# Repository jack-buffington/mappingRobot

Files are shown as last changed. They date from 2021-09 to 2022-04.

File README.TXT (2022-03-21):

This readme was last updated on March 20 2022.

This repository will eventually contain all of the files necessary to make a mapping robot that can map its 
environment using a 2D lidar-like sensor.  At the time of writing this README, the project is 
ongoing.  Eventual goals of this project are:

* Have the robot autonomously map its environment using a RPlidar A2 module.  
* Know when it is done mapping its environment. 
* Do so using ROS.  
* With only a few minor exceptions, run exclusively my own code.
* Have the capability to connect to the robot using a remote computer which can view the current state of the
map as well as to take direct control of the robot.  

The robot system will consist of three processors.  The first is the remote computer which does no 
major computation.  It will be for the user to view the map and to control the state of the robot if necessary.  
The second is an onboard processor that will do the heavy lifting and which holds 
the most up-to-date map.  The third is a microcontroller that handles low-level tasks such as driving the motors, 
reading sensors, and controllng the power to the motors, CPU, and itself. 

Power is supplied to the robot from an off-the-shelf battery pack for Dewalt cordless tools.  

It its current state, the MCU code is pretty much fully functional.  I will likely update it at some point to
read one or more downward-looking range finders so that it doesn't attempt suicide by driving down steps.  It currently
can do the following:
   * Read the battery voltage, display it on the OLED display, and send the voltage to the CPU
   * Read the encoders attached to the motors and send their values to the CPU
   * Drive the motors with a closed-loop velocity controller
   * Play beeps
   * Control the power to the CPU, motors, and itself
   * Communicate through two serial ports.  One to the CPU and one connected to the programming port.
  
The CPU code has:
   RPlidar node - controls a RPlidar A2 and reads its data.  This data is conditionally published based on a divider that 
       Allows it to send every N scans.  
   MCU node - Subscribes to a few topics which can be forwarded to the MCU and publishes a couple others which repeat 
       messages received from the MCU in a ROS-friendly format.  

The Remote computer code has:
   lidar viewer - Ideally I would use RVIZ to see the lidar data but either I don't yet know how to use RVIZ or I have it
	misconfigured so I wrote a quick and dirty program to display the scans.  
   joystick driving node - Lets you control the robot with a joystick if you have teleop_twist_joy installed on your system.

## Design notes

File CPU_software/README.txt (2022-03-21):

To compile, enter the following from this directory:

bash ./compileIt.sh

That script sets the date in case it is wrong so that colcon doesn't complain.  It also deletes previous build files 
so that you end up with something that is based on your most recent code.  It then does the compile.

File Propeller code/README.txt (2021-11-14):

Although they aren't used here, I have also included velocityPID.spin and velocityWithAccelerationTester.spin just for reference.

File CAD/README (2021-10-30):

You can find the most recent CAD model here:
https://cad.onshape.com/documents/e171561c6562339657e2c6d4/w/af4afc644c5b7dbe0063a584/e/c5b0ace67d7282b7c7552f78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

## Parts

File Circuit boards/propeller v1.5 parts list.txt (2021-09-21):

Partlist

Exported from Propeller board rev 1.5.brd at 7/13/2021 8:17 PM

EAGLE Version 9.2.2 Copyright (c) 1988-2018 Autodesk, Inc.

Assembly variant: 

Part                         Value                                            Package                              Library               Position (mil)        Orientation

3.3V_LED                                                                      LED_SML1206                          arduino board rev 1.3 (164 433)             R90
3V3_REGULATOR_FOR_PROPELLER  VOLTAGE_REGULATOR_3_TERMINALXP_POWER_VR05_SERIES VR05_SERIES_VREG                     Jack                  (1717.40157 1269.37008) R180
5V_C_680PF                   680pf                                            JACK_0805                            arduino board rev 1.3 (3220 945)            R180
5V_LED                                                                        LED_SML1206                          arduino board rev 1.3 (2595 945)            R0
5V_LED_R1                    470                                              JACK_0805                            arduino board rev 1.3 (2820 945)            R0
5V_LED_R2                    470                                              JACK_0805                            arduino board rev 1.3 (256 472)             R270
5V_REGULATOR_PULLUP          10K                                              JACK_0805                            arduino board rev 1.3 (3370 1495)           R180
5V_R_220                     220                                              JACK_0805                            arduino board rev 1.3 (3370 945)            R0
BATTERY_VOLTAGE_DIVIDER_HIGH 11K                                              JACK_0805                            arduino board rev 1.3 (2047.42188 1209.86897) R90
BATTERY_VOLTAGE_DIVIDER_LOW  1.6K                                             JACK_0805                            arduino board rev 1.3 (2046.38521 1378.2687) R90
MOTOR_C_680PF                680pf                                            JACK_0805                            arduino board rev 1.3 (3214.46088 289.96518) R180
MOTOR_ENABLE_MOSFET          JACK_MOSFET_N_CHANNELBSS138LCT-ND                JACK_SOT23                           arduino board rev 1.3 (3630.98425 571.22047) R0
MOTOR_ENABLE_MOSFET1         JACK_MOSFET_N_CHANNELBSS138LCT-ND                JACK_SOT23                           arduino board rev 1.3 (3620 1270)           R0
MOTOR_LED                                                                     LED_SML1206                          arduino board rev 1.3 (2595 295)            R0
MOTOR_LED_R                  600                                              JACK_0805                            arduino board rev 1.3 (2820 295)            R0
MOTOR_MOSFET_PULLDOWN        10K                                              JACK_0805                            arduino board rev 1.3 (3630.98425 453.11024) R180
MOTOR_PULLUP                 10K                                              JACK_0805                            arduino board rev 1.3 (3358.70079 845.94488) R180
MOTOR_PULLUP2                10K                                              JACK_0805                            arduino board rev 1.3 (3620 1145)           R180
MOTOR_R_220                  220                                              JACK_0805                            arduino board rev 1.3 (3364.46088 289.96518) R0
MOTOR_TRIM                   13.2K                                            JACK_0805                            arduino board rev 1.3 (3050 290)            R0
R1                           240                                              805_SMD                              jack_custom           (250 314)             R90
R25                          10k                                              805_SMD                              jack_custom           (1170 920)            R0
RTRIM_5V                     16.2K                                            JACK_0805                            arduino board rev 1.3 (3051.48413 945)      R0
U$1                          CONNECTOR_2_PINJST_PH_SERIES                     JST_2_PIN_PH_SERIES                  Jack                  (2160 340)            R180
U$2                          JACK_SCREW_TERMINAL_2_CONDUCTORAMP-282837-2      JACK_AMP-282837-2                    arduino board rev 1.3 (3045 1720)           R0
U$3                          POWER_CONTROLLER_LTC2954-2TSOT-23-8              TSOT-23-8                            Jack                  (2029 479)            R0
U$4                          JACK_DC_TO_DC_VARIABLE_555-1172-1-ND             JACK_DC2DC_555-1172-1-ND             arduino board rev 1.3 (3520 1445)           R180
U$5                          1uf                                              0805                                 Jack                  (2195 470)            R180
U$6                          JACK_SCREW_TERMINAL_2_CONDUCTORAMP-282837-2      JACK_AMP-282837-2                    arduino board rev 1.3 (2345 1720)           R180
U$7                          100K                                             0805                                 Jack                  (2145 620)            R90
U$9                          100K                                             0805                                 Jack                  (2220 620)            R90
U$10                         10K                                              0805                                 Jack                  (1937 634)            R180
U$11                         1000pf                                           0805                                 Jack                  (1190 1240)           R270
U$12                         MOSFET_P_CHANNELSI4431CDY                        SO8                                  Jack                  (2120 920)            R0
U$13                         JACK_SCREW_TERMINAL_2_CONDUCTORAMP-282837-2      JACK_AMP-282837-2                    arduino board rev 1.3 (3720 1720)           R0
U$14                         .1uf                                             0805                                 Jack                  (340 314)             R90
U$15                         CRYSTAL8X4.5_PACKAGE                             CRYSTAL_NX8045GB-5MHZ-STD-CSF-3      Jack                  (800 500)             R270
U$16                         .1uf                                             0805                                 Jack                  (360 1060)            R270
U$17                         JACK_DC_TO_DC_VARIABLE_555-1172-1-ND             JACK_DC2DC_555-1172-1-ND             arduino board rev 1.3 (3520 795)            R180
U$18                         .1uf                                             0805                                 Jack                  (1580 1420)           R0
U$19                         TEST_POINT                                       KEYSTONE_ELECTRONICS_5118_TEST_POINT Jack                  (3670 920)            R0
U$20                         LED0805                                          0805                                 Jack                  (340 474)             R270
U$21                         HEADER_4_PIN_.1"                                 FOUR_.1"_HOLES                       Jack                  (390 740)             R90
U$22                         HEADER_5X2                                       HEADER_5X2_.1"_SPACING               Jack                  (820 1720)            R90
U$23                         CONNECTOR_4_PINJST_PH_SERIES                     JST_4_PIN_PH_SERIES                  Jack                  (1440 370)            R270
U$24                         CONNECTOR_4_PINJST_PH_SERIES                     JST_4_PIN_PH_SERIES                  Jack                  (1230 370)            R270
U$25                         CONNECTOR_4_PINJST_PH_SERIES                     JST_4_PIN_PH_SERIES                  Jack                  (1650 370)            R270
U$26                         CONNECTOR_2_PINJST_.1"                           JST_2_PIN_.1"                        Jack                  (2160 180)            R180
U$27                         10K                                              0805                                 Jack                  (1489 703)            R90
U$28                         10uF                                             1210                                 Jack                  (2470 670)            R90
U$29                         10uF                                             1210                                 Jack                  (2470 1320)           R90
U$30                         10uf                                             1210                                 Jack                  (2470 1120)           R270
U$31                         10uf                                             1210                                 Jack                  (2620 1320)           R90
U$32                         10uf                                             1210                                 Jack                  (2470 470)            R270
U$33                         10uf                                             1210                                 Jack                  (2620 1120)           R270
U$34                         SPEAKERGT-0950RP3                                AUDIO_TRANSDUCER_GT-0950RP3          Jack                  (1720 800)            R90
U$35                         DIODESOD-23/SC-76                                SOD-323/SC-76                        Jack                  (1490 870)            R90
U$36                         TRANSISTOR_NPNMMBT3904                           SOT23                                Jack                  (1340 710)            R180
U$37                         200                                              0805                                 Jack                  (1340 810)            R0
U$38                         CONNECTOR_3_PIN.1"SPACING                        THREE_.1"_HOLES                      Jack                  (3610 170)            R180
U$40                         10uf                                             1210                                 Jack                  (2620 470)            R270
U$41                         10uf                                             1210                                 Jack                  (2620 670)            R90
U$42                         1000pf                                           0805                                 Jack                  (1265 1240)           R90
U$43                         150K                                             0805                                 Jack                  (1120 1320)           R90
U$44                         100K                                             0805                                 Jack                  (1044 1320)           R270
U$45                         CONNECTOR_4_PINJST_PH_SERIES                     JST_4_PIN_PH_SERIES                  Jack                  (1020 370)            R270
U$46                         CONNECTOR_4_PINJST_PH_SERIES                     JST_4_PIN_PH_SERIES                  Jack                  (1670 1670)           R90
U$47                         CONNECTOR_4_PINJST_PH_SERIES                     JST_4_PIN_PH_SERIES                  Jack                  (570 370)             R270
U$48                         PROPELLER_PROGRAMMING_HEADERHOLES                FOUR_.1"HOLES                        Jack                  (1370 1070)           R270
U$49                         CONNECTOR_4_PINJST_PH_SERIES                     JST_4_PIN_PH_SERIES                  Jack                  (1900 1670)           R90
U1                           PARALLAX_PROPELLER                               44LQFP                               jack_custom           (770 1070)            R270
U2                           EEPROM_24XX256                                   8_MSOP                               jack_custom           (1170 770)            R0

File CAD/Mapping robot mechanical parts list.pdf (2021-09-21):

Quantity | Description | part number | Where to order | Alternate order location | Notes
2 Encoder/motor/gearbox combo | TT Motor with Encoder (6V 160RPM 120:1) | https://www.dfrobot.com/product-1457.html?search=TT%20Motor%20with%20Encoder%20%286V%20160RPM%20120%3A1%29
2 Wheels | https://www.dfrobot.com/product-352.html
1 1/4" black acrylic | https://www.amazon.com/gp/product/B01DYSTH3K
8 1 5/8" standoffs | https://www.mcmaster.com/91115A564
4 1" standoffs | https://www.mcmaster.com/91115A133
28 6-32 machine screws | https://www.mcmaster.com/92949A149
4 M3 machine screws | https://www.mcmaster.com/92000A120
4 6-32 lock nuts | https://www.mcmaster.com/91831A007
1 Caster | https://www.amazon.com/gp/product/B010SLSK48
2 motor mounts | https://www.pololu.com/product/2670https://www.robotshop.com/en/solarbotics-gmb39-gear-motor-bracket.html I scavenged my motor mounts from another project. Here are two mounts that I think would work but which aren't like the ones that I am using. You will need to adjust your CAD files to have the mounting holes be in the right places.
4 motor mount screws | Choose these to work with your motor mount
4 motor mount long machine screws | Choose these to work with your motor mount
4 motor mount lock nuts | Choose these to work with your motor mount

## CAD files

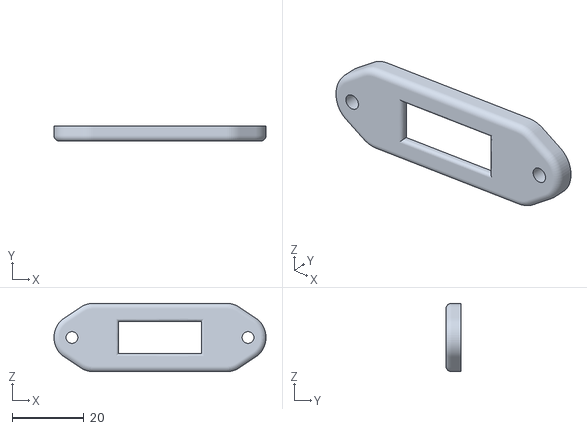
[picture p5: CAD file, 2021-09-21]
CAD/Display bezel.stl
59.0 x 4.20 x 19.0

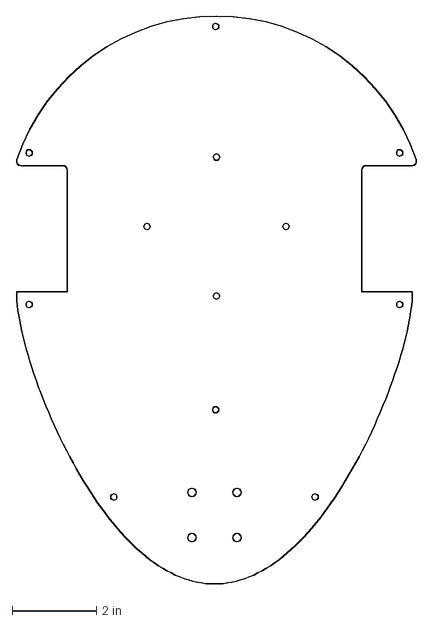
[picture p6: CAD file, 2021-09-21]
CAD/Use for laser cutting/upper chassis plate2_2.DXF
9.51 x 13.5 in

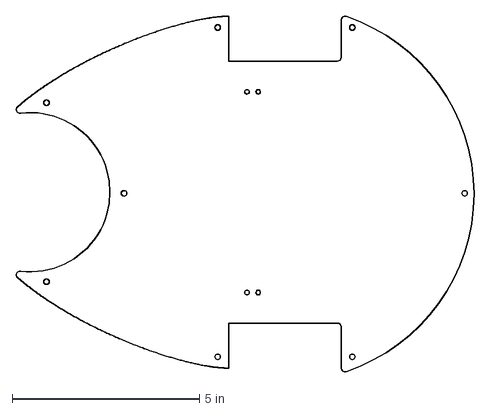
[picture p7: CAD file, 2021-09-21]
CAD/Use for laser cutting/lower chassis plate_2.DXF
12.2 x 9.51 in

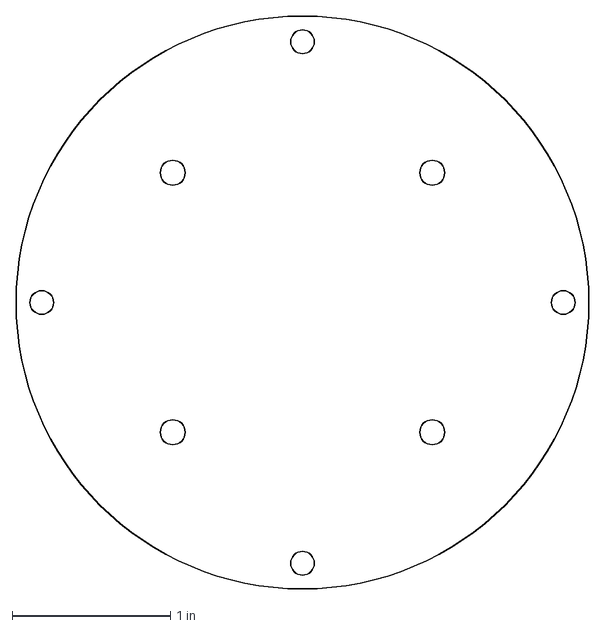
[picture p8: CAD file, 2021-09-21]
CAD/Use for laser cutting/rplidar mount_2.DXF
3.62 x 3.62 in

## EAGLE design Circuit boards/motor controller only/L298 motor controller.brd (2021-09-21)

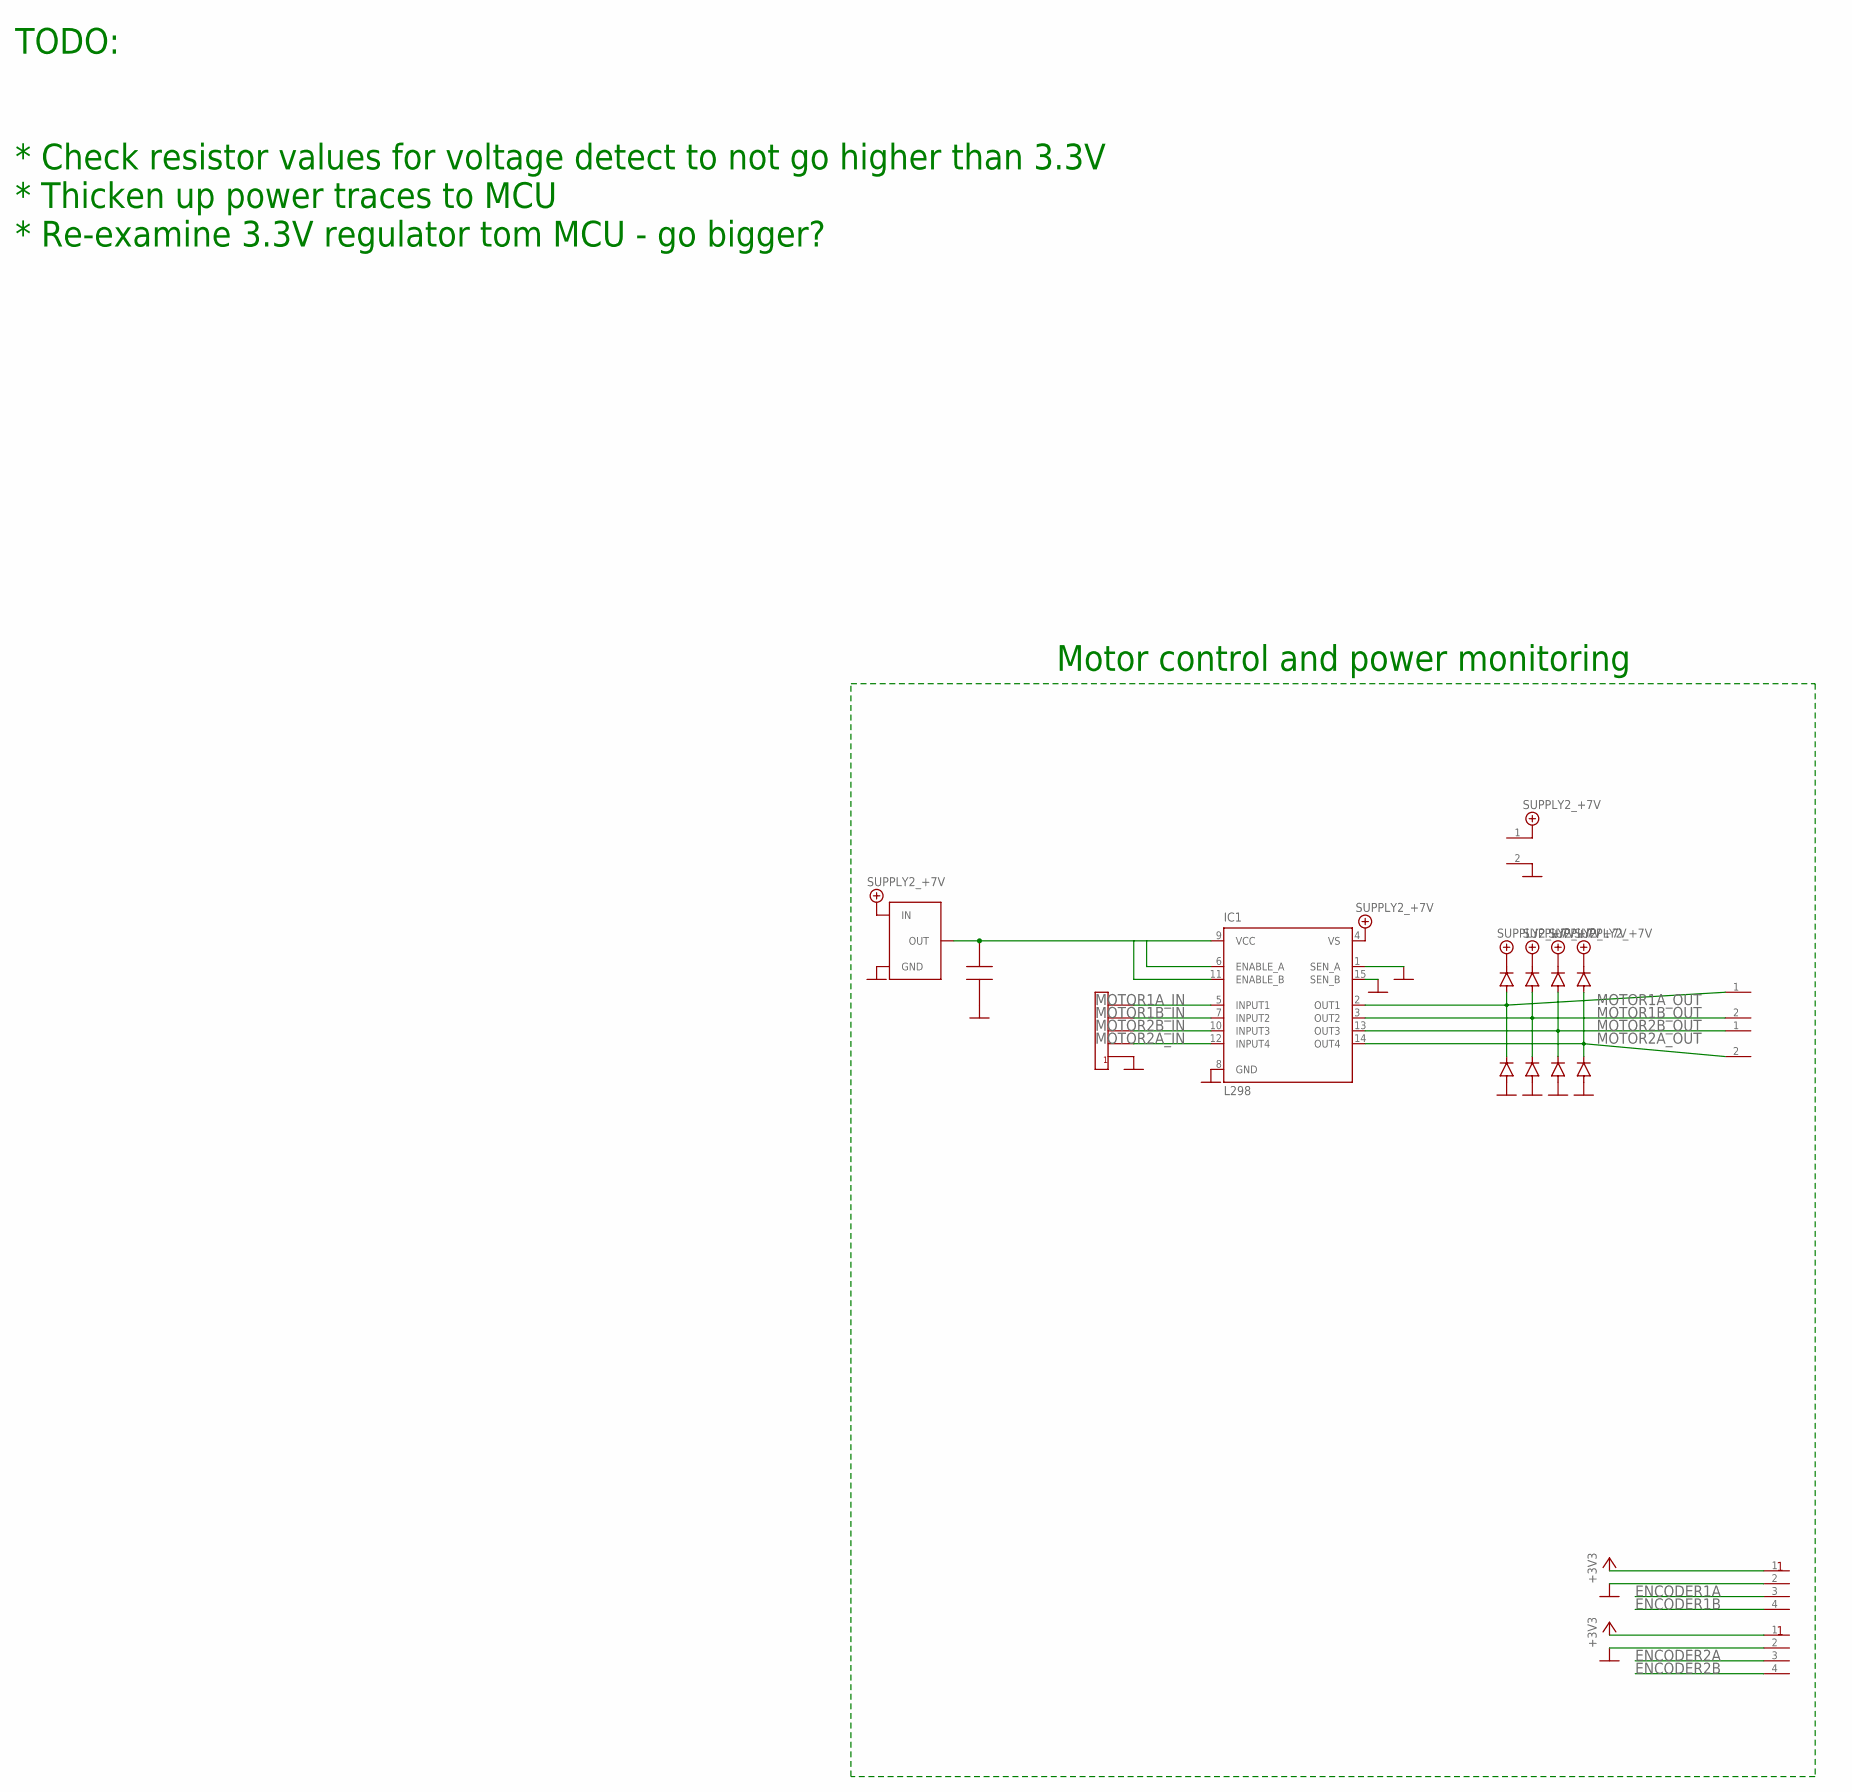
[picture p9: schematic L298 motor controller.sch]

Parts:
IC1: L298; MULTIWATT-15
U$1, U$2, U$4: SCREW_TERMINAL_2_CONDUCTOR_M20109-ND; WM20109-ND
U$3: CONNECTOR_5_PIN; JST_5_PIN_PH_SERIES
U$13, U$14, U$16, U$18, U$19, U$20, U$21, U$22: DIODESOD-123FL; SOD-123FL
U$25: VOLTAGE_REGULATOR_3_TERMINALMCP1799_SOT23; SOT23
U$26: CAPACITOR0805; 0805
U$46, U$49: CONNECTOR_4_PINJST_PH_SERIES; JST_4_PIN_PH_SERIES

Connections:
+3V3: U$46.1, U$49.1
+7V: IC1.4 (VS), U$13.C, U$14.C, U$16.C, U$18.C, U$25.3 (IN)
ENCODER1A: U$46.3
ENCODER1B: U$46.4
ENCODER2A: U$49.3
ENCODER2B: U$49.4
GND: IC1.1 (SEN_A), IC1.8 (GND), IC1.15 (SEN_B), U$3.1, U$19.A, U$20.A, U$21.A, U$22.A, U$25.1 (GND), U$26.P$2 (1+), U$46.2, U$49.2
MOTOR1A_IN: IC1.5 (INPUT1), U$3.5
MOTOR1A_OUT: IC1.2 (OUT1), U$1.1, U$13.A, U$19.C
MOTOR1B_IN: IC1.7 (INPUT2), U$3.4
MOTOR1B_OUT: IC1.3 (OUT2), U$1.2, U$14.A, U$20.C
MOTOR2A_IN: IC1.12 (INPUT4), U$3.2
MOTOR2A_OUT: IC1.14 (OUT4), U$2.2, U$18.A, U$22.C
MOTOR2B_IN: IC1.10 (INPUT3), U$3.3
MOTOR2B_OUT: IC1.13 (OUT3), U$2.1, U$16.A, U$21.C
unnamed: IC1.6 (ENABLE_A), IC1.9 (VCC), IC1.11 (ENABLE_B), U$25.2 (OUT), U$26.P$3 (2-)

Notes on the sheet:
Motor control and power monitoring
TODO: * Check resistor values for voltage detect to not go higher than 3.3V * Thicken up power traces to MCU * Re-examine 3.3V regulator tom MCU - go bigger?

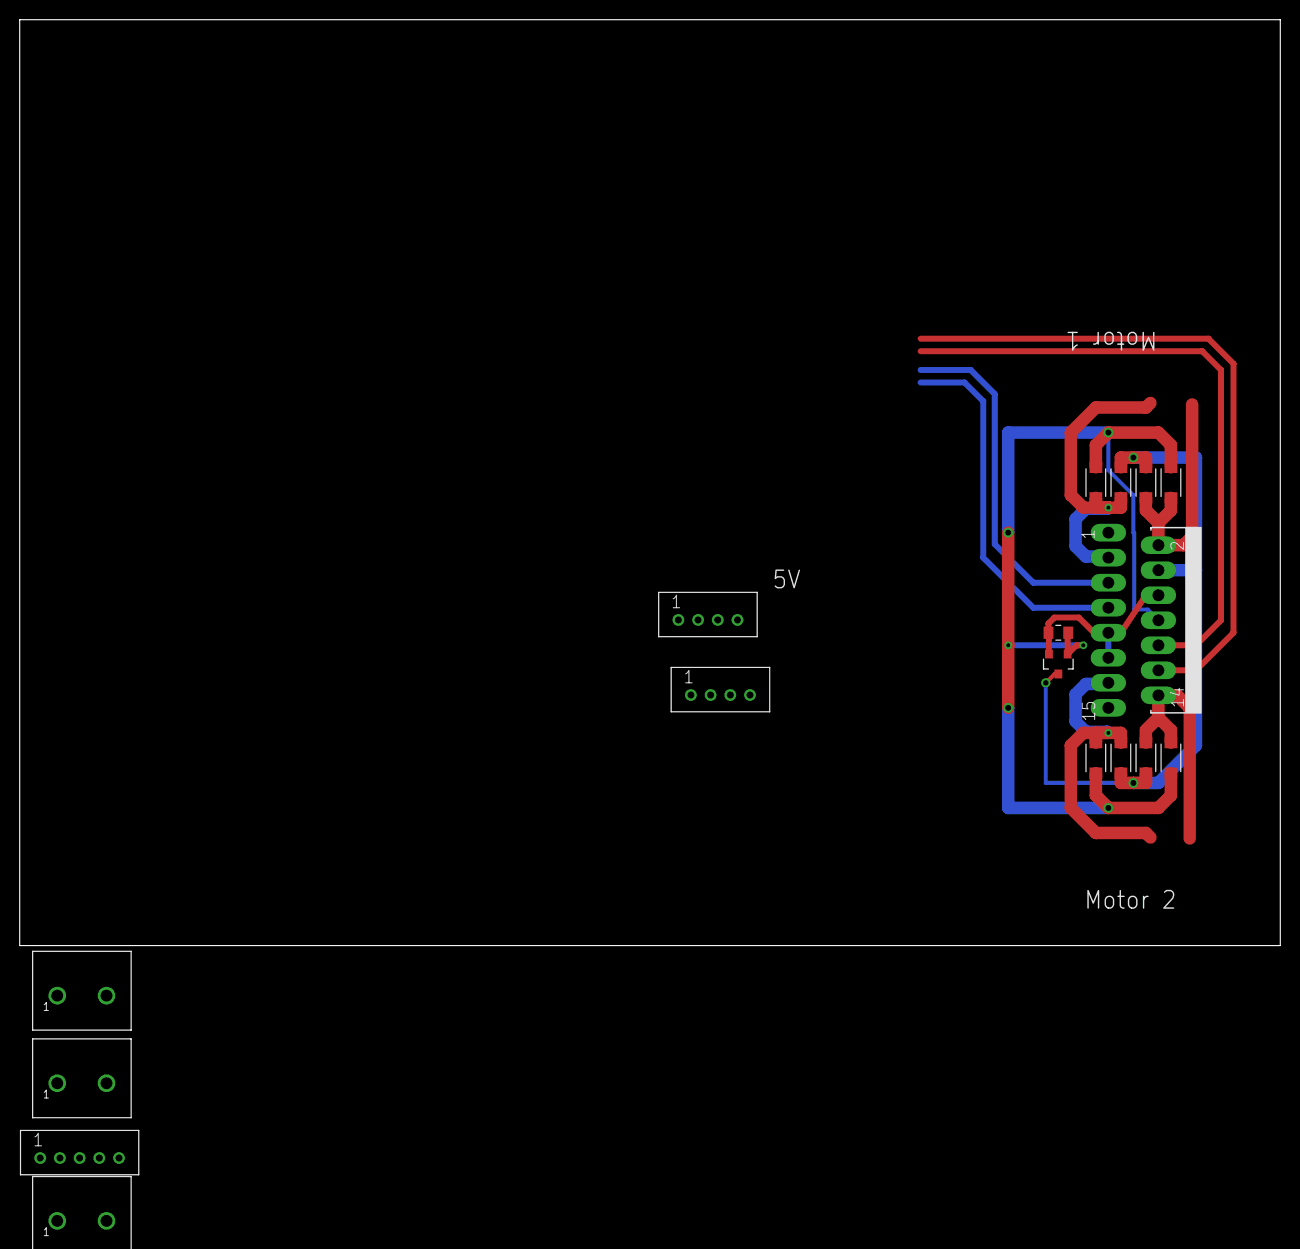
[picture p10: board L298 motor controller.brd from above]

Board: 2 copper layers, 127.9 x 94.0 mm, 17 parts (0 on the bottom side), 12 nets.

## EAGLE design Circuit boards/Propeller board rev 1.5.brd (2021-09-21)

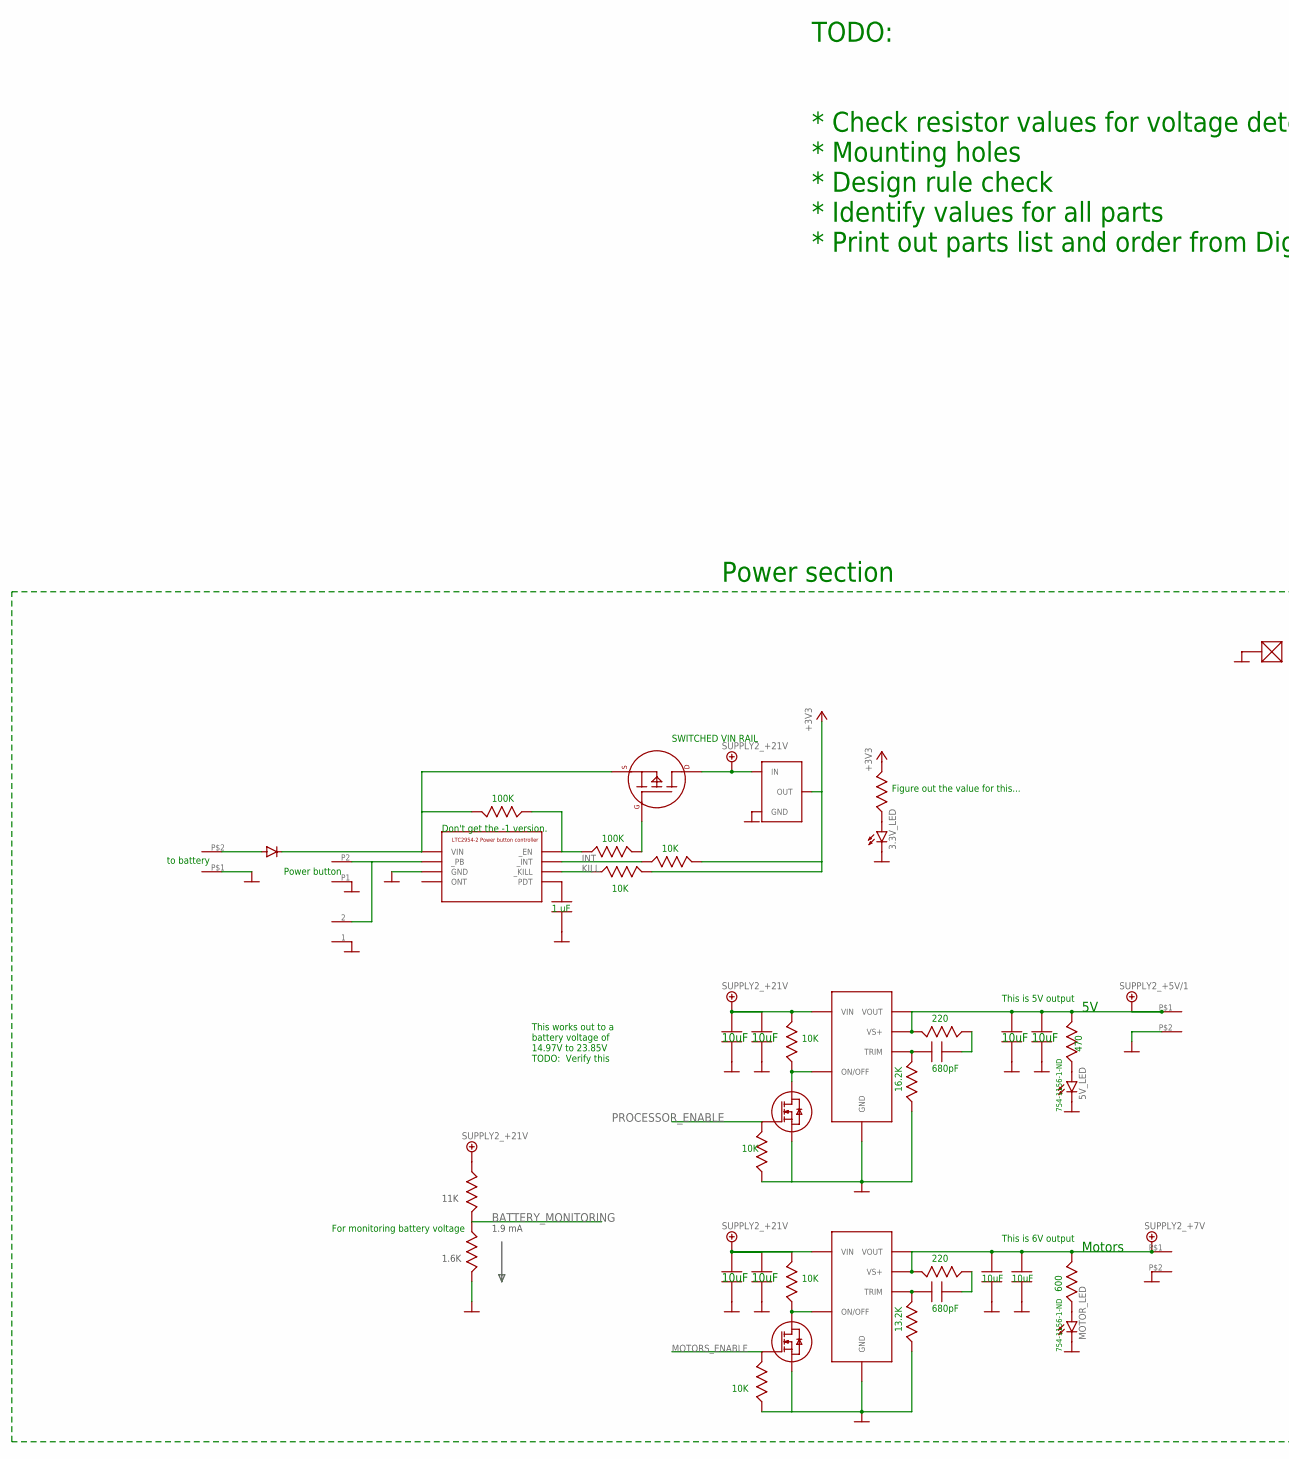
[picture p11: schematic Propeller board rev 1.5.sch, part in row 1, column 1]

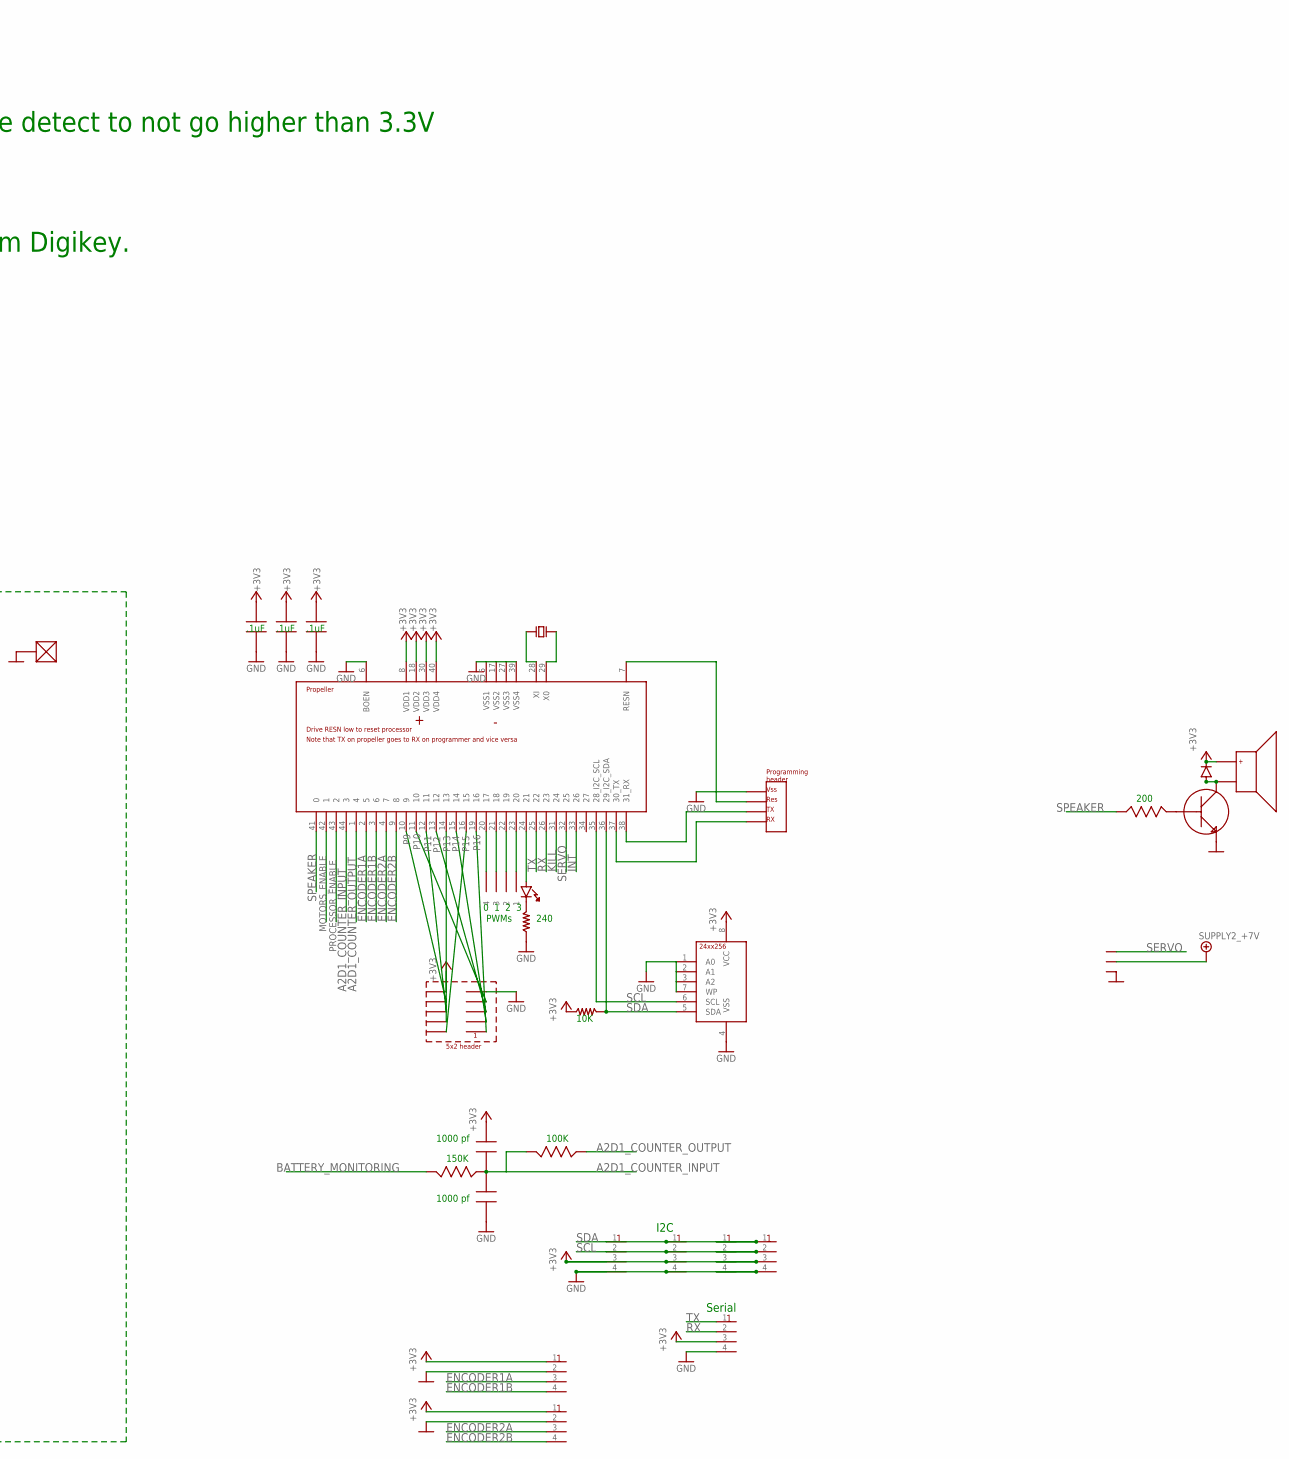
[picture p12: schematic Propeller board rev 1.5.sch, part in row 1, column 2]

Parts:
3.3V_LED, 5V_LED: LED_LEDSML1206; LED_SML1206
3V3_REGULATOR_FOR_PROPELLER: VOLTAGE_REGULATOR_3_TERMINALXP_POWER_VR05_SERIES; VR05_SERIES_VREG
5V_C_680PF: 680pf; JACK_0805
5V_LED_R1, 5V_LED_R2: 470; JACK_0805
5V_REGULATOR_PULLUP: 10K; JACK_0805
5V_R_220: 220; JACK_0805
BATTERY_VOLTAGE_DIVIDER_HIGH: 11K; JACK_0805
BATTERY_VOLTAGE_DIVIDER_LOW: 1.6K; JACK_0805
MOTOR_C_680PF: 680pf; JACK_0805
MOTOR_ENABLE_MOSFET, MOTOR_ENABLE_MOSFET1: JACK_MOSFET_N_CHANNELBSS138LCT-ND; JACK_SOT23
MOTOR_LED: LED_LEDSML1206; LED_SML1206
MOTOR_LED_R: 600; JACK_0805
MOTOR_MOSFET_PULLDOWN: 10K; JACK_0805
MOTOR_PULLUP, MOTOR_PULLUP2: 10K; JACK_0805
MOTOR_R_220: 220; JACK_0805
MOTOR_TRIM: 13.2K; JACK_0805
R1: 240; 805_SMD
R25: 10k; 805_SMD
RTRIM_5V: 16.2K; JACK_0805
U1: PARALLAX_PROPELLER; 44LQFP
U2: EEPROM_24XX256; 8_MSOP
U$1: CONNECTOR_2_PINJST_PH_SERIES; JST_2_PIN_PH_SERIES
U$2, U$6, U$13: JACK_SCREW_TERMINAL_2_CONDUCTORAMP-282837-2; JACK_AMP-282837-2
U$3: POWER_CONTROLLER_LTC2954-2TSOT-23-8; TSOT-23-8
U$4, U$17: JACK_DC_TO_DC_VARIABLE_555-1172-1-ND; JACK_DC2DC_555-1172-1-ND
U$5: 1uf; 0805
U$7, U$9, U$44: 100K; 0805
U$10, U$27: 10K; 0805
U$11: 1000pF or 1nF; 0805
U$12: MOSFET_P_CHANNELSI4431CDY; SO8
U$14, U$16, U$18: .1uf; 0805
U$15: CRYSTAL8X4.5_PACKAGE; CRYSTAL_NX8045GB-5MHZ-STD-CSF-3
U$19: TEST_POINT; KEYSTONE_ELECTRONICS_5118_TEST_POINT
U$20: LED0805; 0805
U$21: HEADER_4_PIN_.1"; FOUR_.1"_HOLES
U$22: HEADER_5X2; HEADER_5X2_.1"_SPACING
U$23, U$24, U$25, U$45, U$46, U$47, U$49: CONNECTOR_4_PINJST_PH_SERIES; JST_4_PIN_PH_SERIES
U$26: CONNECTOR_2_PINJST_.1"; JST_2_PIN_.1"
U$28, U$29: 10uF; 1210
U$30, U$31, U$32, U$33, U$40, U$41: 10uf; 1210
U$34: SPEAKERGT-0950RP3; AUDIO_TRANSDUCER_GT-0950RP3
U$35: DIODESOD523F; SOD523F
U$36: TRANSISTOR_NPNMMBT3904; SOT23
U$37: 200; 0805
U$38: CONNECTOR_3_PIN.1"SPACING; THREE_.1"_HOLES
U$39: DIODEPOWER_DI15; POWER_DI15
U$42: 1000pf or 1 nF; 0805
U$43: 150K; 0805
U$48: PROPELLER_PROGRAMMING_HEADERHOLES; FOUR_.1"HOLES

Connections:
+3V3: 3V3_REGULATOR_FOR_PROPELLER.VOUT (OUT), 5V_LED_R2.P$3, R25.P$1, U1.8 (VDD1), U1.18 (VDD2), U1.30 (VDD3), U1.40 (VDD4), U2.8 (VCC), U$10.C2, U$11.C2 (2-), U$14.C2 (2-), U$16.C2 (2-), U$18.C2 (2-), U$22.P10 (10), U$23.3, U$24.3, U$25.3, U$27.C2, U$34.+, U$35.C, U$45.3, U$46.1, U$47.3, U$49.1
+5V/1: 5V_LED_R1.P$3, 5V_R_220.P$3, U$2.P$1, U$4.VOUT, U$4.VS+, U$30.2 (2-), U$33.2 (2-)
+7V: MOTOR_LED_R.P$3, MOTOR_R_220.P$3, U$13.P$1, U$17.VOUT, U$17.VS+, U$32.2 (2-), U$38.2, U$40.2 (2-)
+21V: 3V3_REGULATOR_FOR_PROPELLER.VIN (IN), 5V_REGULATOR_PULLUP.P$3, BATTERY_VOLTAGE_DIVIDER_HIGH.P$2, MOTOR_PULLUP.P$3, U$4.VIN, U$12.5 (D), U$12.6 (D), U$12.7 (D), U$12.8 (D), U$17.VIN, U$28.2 (2-), U$29.2 (2-), U$31.2 (2-), U$41.2 (2-)
A2D1_COUNTER_INPUT: U1.44 (3), U$11.A1 (1+), U$42.C2 (2-), U$43.A1, U$44.C2
A2D1_COUNTER_OUTPUT: U1.1 (4), U$44.A1
BATTERY_MONITORING: BATTERY_VOLTAGE_DIVIDER_HIGH.P$3, BATTERY_VOLTAGE_DIVIDER_LOW.P$2, U$43.C2
ENCODER1A: U1.2 (5), U$46.3
ENCODER1B: U1.3 (6), U$46.4
ENCODER2A: U1.4 (7), U$49.3
ENCODER2B: U1.9 (8), U$49.4
GND: 3.3V_LED.C, 3V3_REGULATOR_FOR_PROPELLER.GND, 5V_LED.C, BATTERY_VOLTAGE_DIVIDER_LOW.P$3, MOTOR_ENABLE_MOSFET.2 (S), MOTOR_ENABLE_MOSFET1.2 (S), MOTOR_LED.C, MOTOR_MOSFET_PULLDOWN.P$2, MOTOR_PULLUP2.P$2, MOTOR_TRIM.P$2, R1.P$1, RTRIM_5V.P$2, U1.5 (VSS1), U1.6 (BOEN), U1.17 (VSS2), U1.27 (VSS3), U1.39 (VSS4), U2.1 (A0), U2.2 (A1), U2.3 (A2), U2.4 (VSS), U2.7 (WP), U$1.P1, U$2.P$2, U$3.4 (GND), U$4.GND, U$5.A1 (1+), U$6.P$1, U$13.P$2, U$14.A1 (1+), U$16.A1 (1+), U$17.GND, U$18.A1 (1+), U$19.P1, U$22.P9 (9), U$23.4, U$24.4, U$25.4, U$26.1, U$28.1 (1+), U$29.1 (1+), U$30.1 (1+), U$31.1 (1+), U$32.1 (1+), U$33.1 (1+), U$36.2 (E), U$38.1, U$40.1 (1+), U$41.1 (1+), U$42.A1 (1+), U$45.4, U$46.2, U$47.4, U$48.1 (VSS), U$49.2
INT: U1.33 (26), U$3.5 (_INT), U$10.A1
KILL: U1.31 (24), U$3.8 (_KILL), U$27.A1
MOTORS_ENABLE: MOTOR_ENABLE_MOSFET.1 (G), MOTOR_MOSFET_PULLDOWN.P$3, U1.42 (1)
unnamed: U1.7 (RESN), U$48.2 (RES)
unnamed: U1.24 (21), U$20.A1 (A)
unnamed: U$1.P2, U$3.2 (_PB), U$26.2
unnamed: MOTOR_LED.A, MOTOR_LED_R.P$2
unnamed: U$3.1 (VIN), U$7.C2, U$12.1 (S), U$12.2 (S), U$12.3 (S), U$39.3 (C)
unnamed: U$3.7 (PDT), U$5.C2 (2-)
unnamed: U$3.6 (_EN), U$7.A1, U$9.A1
unnamed: MOTOR_ENABLE_MOSFET.3 (D), MOTOR_PULLUP.P$2, U$17.ON/OFF
unnamed: U$9.C2, U$12.4 (G)
unnamed: R1.P$2, U$20.C2 (C)
unnamed: U1.23 (20), U$21.1
unnamed: U1.22 (19), U$21.2
unnamed: U1.21 (18), U$21.3
unnamed: U$34.-, U$35.A, U$36.3 (C)
unnamed: U$36.1 (B), U$37.C2
unnamed: U1.20 (17), U$21.4
unnamed: 5V_C_680PF.P$3 (2), RTRIM_5V.P$3, U$4.TRIM
unnamed: 3.3V_LED.A, 5V_LED_R2.P$2
unnamed: U$6.P$2, U$39.1 (A), U$39.2 (A)
unnamed: U1.38 (31_RX), U$48.3 (TX)
unnamed: 5V_LED.A, 5V_LED_R1.P$2
unnamed: 5V_REGULATOR_PULLUP.P$2, MOTOR_ENABLE_MOSFET1.3 (D), U$4.ON/OFF
unnamed: 5V_C_680PF.P$2 (1), 5V_R_220.P$2
unnamed: MOTOR_C_680PF.P$3 (2), MOTOR_TRIM.P$3, U$17.TRIM
unnamed: MOTOR_C_680PF.P$2 (1), MOTOR_R_220.P$2
unnamed: U1.37 (30_TX), U$48.4 (RX)
unnamed: U1.28 (XI), U$15.1
unnamed: U1.29 (X0), U$15.2
P9: U1.10 (9), U$22.P8 (8)
P10: U1.11 (10), U$22.P7 (7)
P11: U1.12 (11), U$22.P6 (6)
P12: U1.13 (12), U$22.P5 (5)
P13: U1.14 (13), U$22.P4 (4)
P14: U1.15 (14), U$22.P3 (3)
P15: U1.16 (15), U$22.P2 (2)
P16: U1.19 (16), U$22.P1 (1)
PROCESSOR_ENABLE: MOTOR_ENABLE_MOSFET1.1 (G), MOTOR_PULLUP2.P$3, U1.43 (2)
RX: U1.26 (23), U$47.2
SCL: U1.35 (28_I2C_SCL), U2.6 (SCL), U$23.2, U$24.2, U$25.2, U$45.2
SDA: R25.P$2, U1.36 (29_I2C_SDA), U2.5 (SDA), U$23.1, U$24.1, U$25.1, U$45.1
SERVO: U1.32 (25), U$38.3
SPEAKER: U1.41 (0), U$37.A1
TX: U1.25 (22), U$47.1

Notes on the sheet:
to battery
For monitoring battery voltage
Motors
Power section
754-1156-1-ND
11K
1.6K
1.9 mA
This works out to a battery voltage of 14.97V to 23.85V TODO: Verify this
Power button
10K
This is 6V output
This is 5V output
13.2K
16.2K
220
680pF
470
600
SWITCHED VIN RAIL
100K
TODO: * Check resistor values for voltage detect to not go higher than 3.3V * Mounting holes * Design rule check * Identify values for all parts * Print out parts list and order from Digikey.
10uF
I2C
Serial
PWMs
150K
Figure out the value for this...
0 1 2 3
1000 pf
240
200
1 uF
.1uF
Don't get the -1 version.

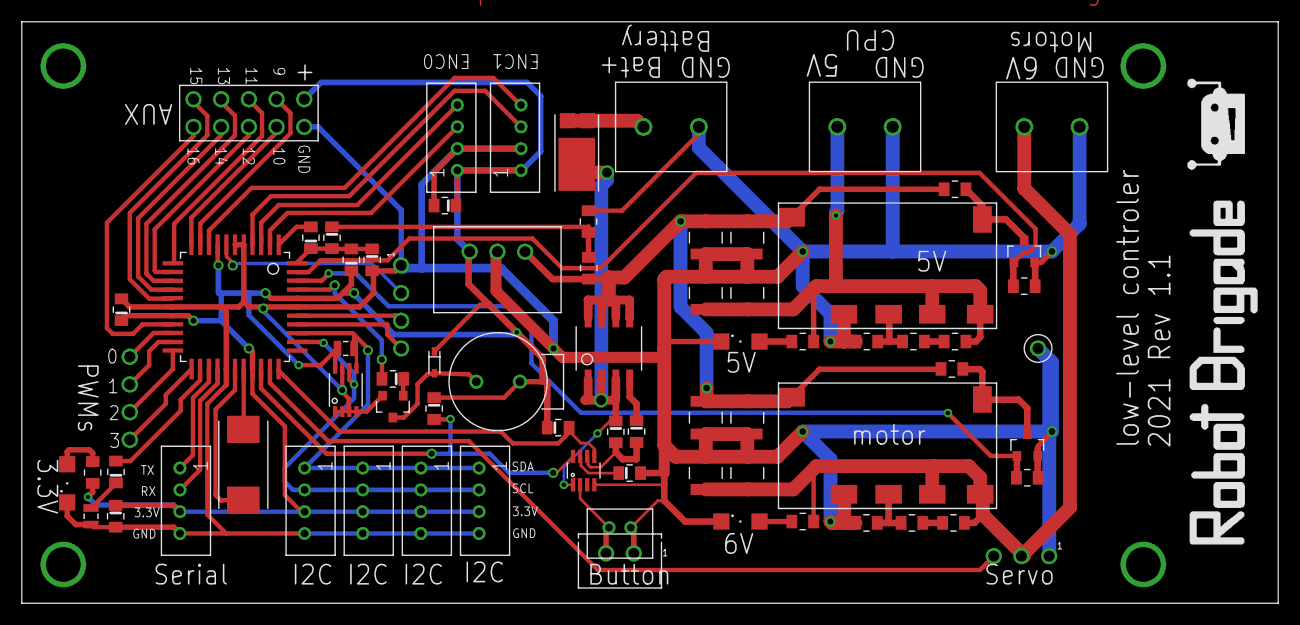
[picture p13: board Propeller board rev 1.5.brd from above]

Board: 2 copper layers, 115.2 x 53.3 mm, 74 parts (0 on the bottom side), 58 nets.

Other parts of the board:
U$8: ROBOT_BRIGADE_LOGO_AND_TEXT_.2"

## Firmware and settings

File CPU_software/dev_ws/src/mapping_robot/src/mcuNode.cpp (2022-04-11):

/*
To get this to run, type the following from inside of the dev_ws directory:
. install/setup.bash
ros2 run mapping_robot mcuNode


"

*/

#include "mcuNode.hpp"




  MCUnode::MCUnode() : Node("mcu_node")
  {
    // Callbacks for things that go to the MCU
    displayMessageSubscription = this->create_subscription<std_msgs::msg::String>("displayMessage", MESSAGE_QUEUE_DEPTH, std::bind(&MCUnode::displayMessageCallback, this, _1));
    driveMotorsSubscription = this->create_subscription<std_msgs::msg::Float32MultiArray>("driveMotors", MESSAGE_QUEUE_DEPTH, std::bind(&MCUnode::driveMotorsCallback, this, _1));
    beepSubscription = this->create_subscription<std_msgs::msg::String>("beep", MESSAGE_QUEUE_DEPTH, std::bind(&MCUnode::beepCallback, this, _1));
    cpuReadySubscription = this->create_subscription<std_msgs::msg::String>("cpuReady", MESSAGE_QUEUE_DEPTH, std::bind(&MCUnode::cpuReadyCallback, this, _1));

    // Callback for monitoring received serial data
    timer_ = this->create_wall_timer(std::chrono::milliseconds(50), std::bind(&MCUnode::serialTimerCallback, this));

    // Publishers that are used when a message is received from the MCU
    voltagePublisher = this->create_publisher<std_msgs::msg::String>("batteryVoltage", MESSAGE_QUEUE_DEPTH);
    buttonPublisher = this->create_publisher<std_msgs::msg::String>("buttonPress", MESSAGE_QUEUE_DEPTH);
    encoderPublisher = this->create_publisher<std_msgs::msg::Float32MultiArray>("wheelEncoders", MESSAGE_QUEUE_DEPTH); 

  }



  void MCUnode::displayMessageCallback(const std_msgs::msg::String::SharedPtr msg) const
  { // to test:  ros2 topic pub -1 /displayMessage std_msgs/msg/String "data: 2~0~testing..."
    RCLCPP_INFO(this->get_logger(), "displayMessage: '%s'", msg->data.c_str());

    std::vector<std::string> splits = splitString(msg->data, "~");  // I chose a tilde because it is unlikely to be in a message
    uint8_t row = atoi(splits[0].c_str());
    uint8_t col = atoi(splits[1].c_str());
    std::string theMessage = splits[2];
    sendTextToDisplay(row,col, theMessage);
  }



  void MCUnode::beepCallback(const std_msgs::msg::String::SharedPtr msg) const
  { // To test:  ros2 topic pub -1 /beep std_msgs/msg/String "data: 0"
    RCLCPP_INFO(this->get_logger(), "beep: '%s'", msg->data.c_str());
    int whichBeep = atoi(msg->data.c_str());
    beep(whichBeep);
  }



  void MCUnode::driveMotorsCallback(const std_msgs::msg::Float32MultiArray::SharedPtr msg) const
  { // to test:  THIS ISN'T CORRECT -> ros2 topic pub -1 /driveMotors2 std_msgs/msg/Float32MultiArray "data: 1.0,1.0"  TODO:  How do I test this manually?
    // The values are in meters per second.

    driveMotors(msg->data[0], msg->data[1]);
  }


  void MCUnode::cpuReadyCallback(const std_msgs::msg::String::SharedPtr msg) const
  {
    RCLCPP_INFO(this->get_logger(), "cpuReady: '%s'", msg->data.c_str());
  }




  void MCUnode::serialTimerCallback()
  {
    // This callback happens 20 times per second.   
    // This implements a state machine that is used to keep track of where it was in a serial message.

    //RCLCPP_INFO(this->get_logger(), "Serial timer callback...");

    static char messageBuffer[32]; // 32 is more than enough I think
    static uint8_t bytesInMessage;
    static uint8_t bytesReceived;
    static uint8_t state = 0;  
    static uint8_t checksum; 

    char theChar;

    while(readCharFromSerialPort(&theChar, 0.001)) // time out in 1 ms.
    {
      // Show the bytes received for debug purposes
      //std::cout << +theChar << ", ";
      switch(state)
      {
        case 0: // Start byte
          if(theChar == 85)
          {
            state = 1;
            checksum = 0;
            bytesReceived = 0;
          }
          break;
        case 1: // bytes in message
          bytesInMessage = theChar;
          state = 2;
          break;
        case 2:
          messageBuffer[bytesReceived] = theChar;
          checksum ^= theChar;
          ++bytesReceived;
          if(bytesReceived == bytesInMessage)
          {
            if(checksum == 0)
            { // Then it has passed the checksum
              state = 0;
              uint8_t messageType = messageBuffer[0];
              switch (messageType)
              {
                case 1: // Button presses
                  {
                  // '0x55 <bytes in message> 0x01 <number of button presses> <checksum>
                  std::cout << "Received a button press message.  " << +messageBuffer[1] << " presses.\n";
                  // Publish this on a topic. 
                  auto message = std_msgs::msg::String();
                  message.data = "Number of button presses: " + std::to_string(messageBuffer[1]);
                  std::cout << "Publishing the button press.\n";
                  buttonPublisher->publish(message);
                  break;
                  }

                case 2: // Battery voltage - This is received periodically whether I want it or not. :)
                  {
                  // Battery voltage is four bytes and represents voltage * 1000
                  uint32_t voltageValue = messageBuffer[1] + (messageBuffer[2] << 8) + (messageBuffer[3] << 16) + (messageBuffer[4] << 24);
                  float voltageFloat = voltageValue;
                  voltageFloat /= 1000;
                  std::cout << "Received a voltage message: " << voltageFloat << "V\n"; 
                  // Publish this on a topic. 
                  auto message = std_msgs::msg::String();
                  message.data = "Battery voltage: " + std::to_string(voltageFloat);
                  std::cout << "Publishing the voltage\n";
                  voltagePublisher->publish(message);
                  break;
                  }
                case 3: // encoder message - This is periodically received as well.  As of writing this, it is being sent every 1/5th of a second.
                  {
                  // Two 32-bit values are sent, which represent the change since last time for the two encoders
                  typeConverter t;

                  t.bytes[0] = messageBuffer[1];
                  t.bytes[1] = messageBuffer[2];
                  t.bytes[2] = messageBuffer[3];
                  t.bytes[3] = messageBuffer[4];
                  int32_t encoder0 = t.s32;

                  t.bytes[0] = messageBuffer[5];
                  t.bytes[1] = messageBuffer[6];
                  t.bytes[2] = messageBuffer[7];
                  t.bytes[3] = messageBuffer[8];
                  int32_t encoder1 = t.s32;
                  
                  // Publish this on a topic.         
                  float encoder0float = encoder0;
                  float encoder1float = encoder1;

                  // Convert the encoder values to meters, also correct for them being negative 
                  // To find this conversion, I did four runs between two and three meters and averaged the result.  
                  encoder0float /= -TICKS_PER_METER;  // This one is negative because the motor is flipped around in the robot.  
                  encoder1float /= TICKS_PER_METER; 
                  std::cout << "wheelEnoders: " << encoder0float << ",\t\t" << encoder1float << std::endl;


                  std_msgs::msg::Float32MultiArray msg;
                  msg.data.push_back(encoder0float);
                  msg.data.push_back(encoder1float);
                  encoderPublisher->publish(msg);
                  break;
                  }
              }
            }
          }
      } // End of the switch statement - No bracket is missing above.  
    }
  }








int main(int argc, char * argv[])
{
  std::cout << "version 021\n";
  std::string portString = "/dev/serial1";
  if(setupSerialPort((char*)portString.c_str(), true))
  {
    std::cout << "Successfully opened the serial port!\n";
  }


  rclcpp::init(argc, argv);
  rclcpp::spin(std::make_shared<MCUnode>());
  rclcpp::shutdown();
  return 0;
}









void beep(int whichBeep)
{  // Causes the MCU to beep in the requested pattern
   // 0xAB <bytes in message> 0x01 <which beep pattern> <checksum>
   uint8_t messageBuffer[5];
   messageBuffer[0] = 171; // 0xAB
   messageBuffer[1] = 3;
   messageBuffer[2] = 1;
   messageBuffer[3] = whichBeep;
   computeChecksum(messageBuffer, sizeof(messageBuffer));
   sendBufferToSerialPort(messageBuffer, sizeof(messageBuffer));  
   flushSerialPort();
}




void sendTextToDisplay(int row, int col, std::string theText)
{  // 0xAB <bytes in message> 0x00 <row> <column> <message> <checksum>
  std::cout << __func__ << std::endl;

   // Do some prep first
   int bytesInMessage = theText.length();
   bytesInMessage += 4; // +4 for message type, row, col, and checksum

   uint8_t messageBuffer[32]; // bigger than it needs to be;

   messageBuffer[0] = 171; //0xAB
   messageBuffer[1] = bytesInMessage;
   messageBuffer[2] = 0;   // display message
   messageBuffer[3] = row;
   messageBuffer[4] = col;
   int msgPos = 5;
   for(unsigned int I = 0; I < theText.length(); ++I)
   {
      messageBuffer[msgPos++] = theText.at(I);
   }

   computeChecksum(messageBuffer, bytesInMessage + 2);
   sendBufferToSerialPort(messageBuffer, bytesInMessage + 2);  
   flushSerialPort();
}



void driveMotors(float leftMotor, float rightMotor)
{  // Drives the motors in meters per second
   // 0xAB <bytes in message> 0x03 <left velocity in ticks per second as long> <right velocity in ticks per second as long><checksum>

   // Convert from meters per second to ticks per second
   int leftMotorInt = leftMotor * TICKS_PER_METER;
   int rightMotorInt = rightMotor * TICKS_PER_METER;

   union intSplitter
   {
      int32_t  theInt;
      char  theChars[4];
   };

   intSplitter splitter;

   uint8_t messageBuffer[12];
   messageBuffer[0] = 171; // 0xAB
   messageBuffer[1] = 10;  // bytes in message
   messageBuffer[2] = 3;   // drive motors

   splitter.theInt = leftMotorInt;
   messageBuffer[3] = splitter.theChars[0];
   messageBuffer[4] = splitter.theChars[1];
   messageBuffer[5] = splitter.theChars[2];
   messageBuffer[6] = splitter.theChars[3];

   splitter.theInt = rightMotorInt;
   messageBuffer[7] = splitter.theChars[0];
   messageBuffer[8] = splitter.theChars[1];
   messageBuffer[9] = splitter.theChars[2];
   messageBuffer[10] = splitter.theChars[3];

   computeChecksum(messageBuffer, sizeof(messageBuffer));
   sendBufferToSerialPort(messageBuffer, sizeof(messageBuffer));  
   flushSerialPort();
}

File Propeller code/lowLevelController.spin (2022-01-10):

' The difference between this version and version 2 is that this version
' doesn't block when it is looking for serial data so other things can happen
' simultaneously.



' Message types to CPU:
' 0: Tells CPU to shutdown because battery is getting low.
' 1: Button press
' 2: Battery voltage
' 3: encoder message


' Message types from CPU
' 0: display message
' 1: beep
' 3: drive motors
' 5: CPU shutting down
' 6: request battery voltage
' 7: CPU ready

CON
    _CLKMODE = xtal1 + pll16x
    _XINFREQ = 5_000_000
    
    BATTERY_DEAD = 14000    ' This is the voltage where my Dewalt drill shuts off
    BATTERY_LOW = 14300     ' This is the voltage where it tells the CPU to shut down
    BATTERY_FULL = 20000
    
    
    LED =  21
    POWER_ON = 24 ' Normally high.  Set low to turn off the system power. 
    BUTTON = 26 ' 0 when button is pushed
    SPEAKER = 0
    PROCESSOR_ENABLE = 2
    MOTOR_ENABLE = 1
    PWM0PIN = 17
    PWM1PIN = 18
    PWM2PIN = 19
    PWM3PIN = 20
    CPU_RX = 23
    CPU_TX = 22
    CPU_POWER_SIGNAL = 9    ' high when power is on.



OBJ
    'Motor control stuff
    PWM         : "PWM.spin"
    SERIAL      : "quadSerialPorts.spin"
    ENCODER     : "encoder.spin"
    PID         : "velocityWithAccelerationPID.spin"
    
    ADC         : "sigmaDelta.spin"
    
    
    
    I2C        : "I2C PASM driver v1.8od.spin"
    OLED       : "SSD1306_fast.spin"                ' This one doesn't take a COG
    

    

VAR
    '=================================================================================================
    ' This group of variables is used by the PWM, encoder, and PID programs and must be kept together.                        
    long    spinAcceleration                             
    long    spinRequestedVelocity0  ' Encoder ticks per high-level timeslot
    long    spinRequestedVelocity1
    long    Pterm
    long    Iterm
    long    Dterm
    long    numberOfEncoders
    long    encoderBasePin
    long    spinEncoderPosition0
    long    spinEncoderPosition1
    long    PWM0
    long    PWM1
    long    PWM2
    long    PWM3
    long    PWMstartPin
    '=================================================================================================
    
    long    stillWorking
    long    waitTime
    long    temp
    long    temp1
    long    temp2
    long    temp3
    long    temp4
    long    batteryValue
    long    bytesInMessage
    long    messageType
    long    bufferPos
    long    checksum
    long    lastButtonState
    
    long    buttonPushes
    long    lastPushTime
    long    countUpdated
    
    long    serialRXstate
    long    serialMessageLength
    long    serialBytesReceived
    long    serialBuffer[30]
    long    serialChecksum

    long    shutdownMessageHasBeenSent
    
    long    voltageCheckTime
    long    voltageCheckWindow
    long    voltageCheckCount
    
    long    encoderCheckTime
    long    encoderCheckWindow
    long    lastEncoder0
    long    lastEncoder1


PUB main
  OUTA[POWER_ON] := 1 ' Make sure the power stays on  
  DIRA[POWER_ON] := 1 ' Make the pin be an output

  DIRA[LED] := 1 ' Set the LED pin to an output
  DIRA[SPEAKER] := 1
  DIRA[BUTTON] := 0 ' this is an input
  DIRA[MOTOR_ENABLE] := 1
  DIRA[PROCESSOR_ENABLE] := 1
  DIRA[CPU_POWER_SIGNAL] := 0 ' Make it an input

  
  
  OUTA[MOTOR_ENABLE] := 1 'Turn on the motor power
  OUTA[PROCESSOR_ENABLE] := 1 'Turn on the CPU
  
  shutdownMessageHasBeenSent := 0
 
  start_uarts
  serial.str(0,string("Starting up...",13))
  
  
  I2C.start(28, 29, 400000)
  oled.start($3C) ' The I2C start command is tucked into here

  oled.displayOn
  serial.str(0,string("Display is now on",13))
    
  oled.setPageMode
  
  
  
  oled.setTextRowCol(0,0)
  oled.putString(string(" Mapping robot  "))
  oled.setTextRowCol(1,0)
  oled.putString(string(" Waiting for CPU"))
  oled.setTextRowCol(2,0)
  oled.putString(string("                "))
  oled.setTextRowCol(3,0)
  oled.putString(string("                "))
  

  ADC.Start_ADC(@batteryValue)

  playHappyBeeps
  
  
  ' Set up stuff for PWM
  PWMstartPin := 17
  pwm.start(@PWM0)
  
  ' Set up stuff for the encoders
  numberOfEncoders := 2     ' I want two encoders
  encoderBasePin := 5       ' Encoder 1 attached to pins 5 & 6  Encoder 2 attached to pins 7 & 8
  spinEncoderPosition0 := 0     ' Initial encoder value
  spinEncoderPosition1 := 0                           
  ENCODER.start(@numberOfEncoders) 
  lastEncoder0 := 0
  lastEncoder1 := 0
  
  
  ' Start up the velocity controller
  Pterm := 10      
  Iterm := 6
  Dterm := 30
  spinRequestedVelocity0 := 0
  spinRequestedVelocity1 := 0
  spinAcceleration := 5000
  PID.start(@spinAcceleration)
  
  stillWorking := 1
  
  lastButtonState := 0
  buttonPushes := 0
  
  countUpdated := 0
  lastPushTime := CNT  
  
  
  serialRXstate := 0
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

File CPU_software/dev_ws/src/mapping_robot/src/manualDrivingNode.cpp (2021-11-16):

/*
To get this to run, type the following from inside of the dev_ws directory:
. install/setup.bash
  


"

*/

#include "manualDrivingNode.hpp"




  manualDrivingNode::manualDrivingNode() : Node("manual_driving_node")
  {
    // Callback for monitoring the keyboard
    timer_ = this->create_wall_timer(std::chrono::milliseconds(50), std::bind(&manualDrivingNode::keyboardCallback, this));

    // Publisher so that I can send out motor messages
    motorPublisher = this->create_publisher<std_msgs::msg::Float32MultiArray>("driveMotors", MESSAGE_QUEUE_DEPTH);
  }




  void manualDrivingNode::keyboardCallback()
  {
    // This callback happens 20 times per second. It checks for keyboard input  
    char c;
    static char lastC = 0;
    static bool stopSent = true;
    static float speed = 0.1;
    float leftMotor = 0;
    float rightMotor = 0;

    while(kbhit()) // If a key has been pressed
    {
      startTiming();
      c = getchar();
      if (lastC != c)
      {
        stopSent = false;
        switch (c)
        {
          case('a'):
            std::cout << "left turn\n";
            leftMotor = -speed;
            rightMotor = speed;
            std::cout << "Motors: " << leftMotor << ", " << rightMotor  << std::endl;
            publishMotorMessage(leftMotor, rightMotor);
            break;
          case('w'):
            std::cout << "forward\n";
            leftMotor = speed;
            rightMotor = speed;
            std::cout << "Motors: " << leftMotor << ", " << rightMotor  << std::endl;
            publishMotorMessage(leftMotor, rightMotor);
            break;
          case('d'):
            std::cout << "right turn\n";
            leftMotor = speed;
            rightMotor =- speed;
            std::cout << "Motors: " << leftMotor << ", " << rightMotor  << std::endl;
            publishMotorMessage(leftMotor, rightMotor);
            break;
          case('s'):
            std::cout << "backward\n";
            leftMotor = -speed;
            rightMotor = -speed;
            std::cout << "Motors: " << leftMotor << ", " << rightMotor  << std::endl;
            publishMotorMessage(leftMotor, rightMotor);
            break;
          case(' '):
            std::cout << "stop\n";
            leftMotor = 0;
            rightMotor = 0;
            std::cout << "Motors: " << leftMotor << ", " << rightMotor  << std::endl;
            publishMotorMessage(leftMotor, rightMotor);
            break;

          // The speeds are meant to change things between directional button pushes, not when one is being actively being pushed.
          case('1'):
            std::cout << "Speed 0.1\n";
            speed = 0.1;
            break;
          case('2'):
            std::cout << "Speed 0.25\n";
            speed = 0.25;
            break;
          case('3'):
            std::cout << "Speed 0.5\n";
            speed = 0.5;
            break;
          case('4'):
            std::cout << "Speed 1.0\n";
            speed = 1.0;
            break;
          case('5'):
            std::cout << "Speed 1.5\n";
            speed = 1.5;
            break;
          case('6'):
            std::cout << "Speed 2.0\n";
            speed = 2.0;
            break;
          case('7'):
            std::cout << "Speed 3.0\n";
            speed = 3.0;
            break;
          case('8'):
            std::cout << "Speed 4.0\n";
            speed = 4.0;
            break;



        }
        
      }
      lastC = c;
    } // end of while statement

    //std::cout << "time:" << getElapsedTimeInMilliseconds() << std::endl << std::flush;
   //usleep(10000); // 10 ms
    if(getElapsedTimeInMilliseconds() > KEY_DELAY && stopSent == false)
    {
      stopSent = true;
      std::cout << "STOP\n";
      publishMotorMessage(0,0);
      lastC = 0;
      leftMotor = 0;
      rightMotor = 0;
    }
    
  }


void manualDrivingNode::publishMotorMessage(float leftMotor, float rightMotor)
{
    std_msgs::msg::Float32MultiArray msg;
    msg.data.push_back(leftMotor);
    msg.data.push_back(rightMotor);
    motorPublisher->publish(msg);
}






int main(int argc, char * argv[])
{
  std::cout << "Version 002 - Uses the Float32MultiArray instead of a string.\n";

  turnOffLocalEcho();
  startTiming();

  rclcpp::init(argc, argv);
  rclcpp::spin(std::make_shared<manualDrivingNode>());
  rclcpp::shutdown();
  return 0;
}

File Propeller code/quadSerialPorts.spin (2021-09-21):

{{  FullDuplexSerial4portPlus version 1.01
  - Tracy Allen (TTA)   (c)22-Jan-2011   MIT license, see end of file for terms of use.  Extends existing terms of use.
  - Can open up to 4 independent serial ports, using only one pasm cog for all 4.
  - Supports flow control and open and inverted baud modes
  - Individually configurable tx and rx buffers for all 4 ports, any size, set in CONstants section at compile time
  - Part of the buffer fits within the object's hub footprint, but even so the object is restartable
  - Buffers are DAT type variables, therefore a single instance of the object can be accessed throughout a complex project.

  - Modified from Tim Moore's pcFullDuplexSerial4fc, with further motivation and ideas from Duane Degn's pcFullDuplexSerial4fc128
  - Changes and bug fixes include:
    - Flow control is now operational when called for, with correct polarity (bug correction)
    - Jitter is reduced, unused ports are properly skipped over (bug correction), operation speed is increased.
    - Stop bit on reception is now checked, and if there is a framing error, the byte is not put in the buffer.
    - Buffer sizes are arbitrary, each port separate rx & tx up to available memory
       Changes in pasm and in Spin methods to accomodate larger buffers, major reorganization of DAT section.
    - Added strn method for counted string, and rxHowFull method for buffer size.
    - Cut out most of the format methods such as DEC and HEX, expecting those to be their own object calling rx, tx, str and strn methods.
      See companion object DataIO4port.spin in order to maintain compatibility with methods in the original pcFullDuplexSerial4fc.

  - 1v01
    - init method returns pointer @rxsize, for data buffers and data structure.
  - 1v00
    - documentation
  - 0v91
    - restored DEFAULTTHRESHOLD constant
    - made default buffer sizes in the DAT section rather than init
    - removed the numeric methods to their own companion object, dataIO4port.
  - 0v3
    - first public release with the jitter and flow control issues fixed, and large buffers.

  Links:
  Development of this version:
  --- http://forums.parallax.com/showthread.php?137349-yet-another-variant-fullDuplexSerial4portplus
  Tim Moore's original pcFullDuplexSerial4fc and updates to allow flow control:
  --- http://forums.parallaxinc.com/forums/default.aspx?f=25&p=1&m=273291#m276667
  --- http://obex.parallax.com/objects/340/      7/24/08 version
  --- http://forums.parallaxinc.com/forums/default.aspx?f=25&p=1&m=349173    8/14/08 update, flow polarity correction, not in obex
  Duane Degn's thread, larger 128 or 512 byte buffers and reusing buffer space, discussion of issues
  --- http://forums.parallax.com/showthread.php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
  Juergen Buchmueller, 2 port trimmed down version
  --- http://forums.parallax.com/showthread.php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
  Serial Mirror, single port but same idea regarding buffers in the DATa space
  --- http://forums.parallax.com/showthread.php?94311-SerialMirror-A-FullDuplexSerial-enhancement
  --- http://obex.parallax.com/objects/189/
  Re baud rates attainable, hiccups:
  --- http://forums.parallaxinc.com/forums/default.aspx?f=25&p=1&m=282923#m282978
  --- http://forums.parallaxinc.com/forums/default.aspx?f=25&p=1&m=334784
  --- http://forums.parallax.com/showthread.php?120868-FullDuplexSerial-hiccups
  Jitter, discussions of jitter in different Prop serial programs, PhiPi's development of PBnJ full duplex:
  --- http://forums.parallax.com/showthread.php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
  --- http://forums.parallax.com/showthread.php?136431-Serial-objects-question
  Humanoido's catalog of serial port objects
  --- http://forums.parallax.com/showthread.php?128184-Serial-Objects-for-SPIN-Programming
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

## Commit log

2021-09-21 Initial commit of new code and files.
    [Display bezel.stl, L298 motor controller.brd, L298 motor controller.sch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]
2021-11-14 Added a couple of faster driving speeds.
2021-11-16 Switched from string to float[] for driveMotors
2022-01-10 Add encoder message
2022-04-11 Fix joystick driving issue
    [mcuNode.cpp]

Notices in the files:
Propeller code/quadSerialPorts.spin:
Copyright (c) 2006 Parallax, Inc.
